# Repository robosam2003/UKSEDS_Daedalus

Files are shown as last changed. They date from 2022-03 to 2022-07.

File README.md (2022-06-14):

# UKSEDS Team Daedalus - "In thrust we trust"

The rocket avionics consisted of a Teensy 4.1 for the main microcontoller, a low-g IMU (BNO055), a high-g accelerometer (ADXL377), a pressure sensor (BMP280), a GPS (NEO-6M) and a 433 MHz radio transciever (RFM96W).

The purpose of the rocket was to collect acceleration and gyroscope data such that we could test our IMU based position estimation algorithm (also called dead reckoning).

# Code
The `code` folder contains code for all the sensors and telemetry onboard and for the ground station. The `masterCode` folder contains the final code loaded onto the rocket.

## Sensors and telemetry:
- **BNO055**: Our low-g IMU, containing accelerometers capable of ±16G, as well as very accurate gyroscopes and magnetometers. Big thanks to SunrIde's [Tom Danvers](https://github.com/TomD53) for writing the library we used to interface with the BNO055: [`Arduino-BNO055`](https://github.com/TeamSunride/Arduino-BNO055). 
- **ADXL377**: Our high-g IMU, capable of up to ±200G. This is an analogue sensor and is *very noisy*, so both hardware filters (capacitors) and software filters ([Kalman filters](https://github.com/denyssene/SimpleKalmanFilter)) were used to get accurate data. 
- **BMP280**: A pressure based altimeter used in conjunction with the brilliant [Adafruit library](https://github.com/adafruit/Adafruit_BMP280_Library).
- **NEO-6M**: A cheap but capable GPS module from ublox. In order to get a fast GPS lock, we implemented assisted GPS loading using the ublox AssistNow service. See [`code/NEO6mWithAssistNow`](https://github.com/robosam2003/UKSEDS_Daedalus/tree/main/code/NEO6mWithAssistNow).
- **RFM96W**: A 433MHz SX1272 based tranciever module that was used both onboard and on our ground station. We used the LoRa protocol for greater range. We implemented an interrupt driven method using [`RadioLib`](https://github.com/jgromes/RadioLib).

## Ground station
The ground station used an old arduino nano with the RFM96W to recieve live telemetrics from the rocket. The launch commit button was used to put the rocket into a launch ready state remotely.

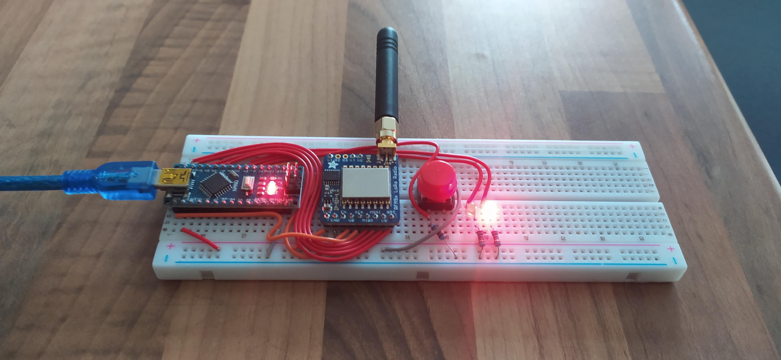
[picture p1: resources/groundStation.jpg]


It passed this data to Grafana and InfluxDB using the [line protocol](https://docs.influxdata.com/influxdb/cloud/reference/syntax/line-protocol/). Big thanks to SunrIde's [Yomi](https://github.com/abayomi185), [Tom](https://github.com/TomD53) and [Sebastiano](https://github.com/robosam2003/UKSEDS_Daedalus/blob/main/resources/grafanaDashboard.jpg) for building the software to do this [`TeamSunride/GroundStation`](https://github.com/TeamSunride/GroundStation). Our live telemetry Grafana Dashboard is shown below:

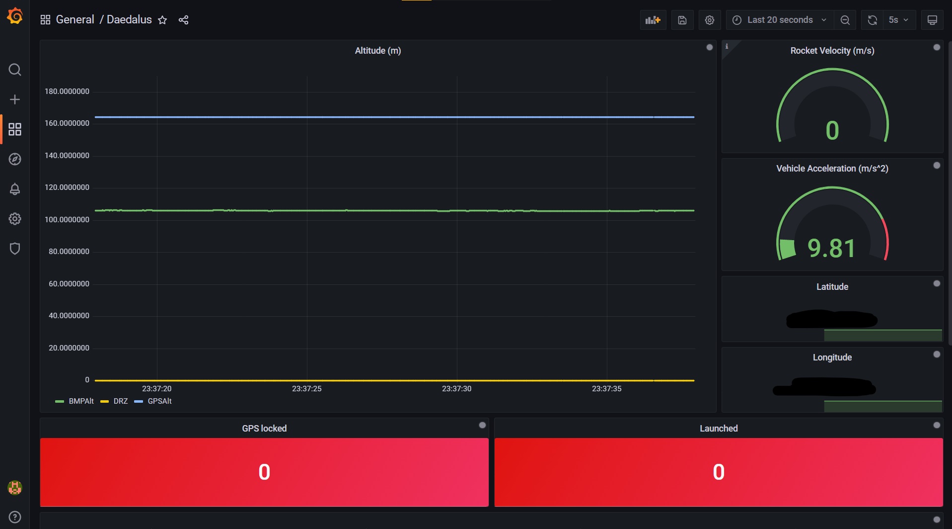
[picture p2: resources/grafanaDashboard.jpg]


### The rocket launch sequence is as follows:
- Ensure ground station is booted and ready.
- **Compile** masterCode/main.cpp and upload to teensy so that the RTC syncs.
- Setup sensors, datalogging and telemety on the ground.
- Full system test with serial output to double check sensor values look reasonable.
- Load avionics into rocket.
- Wait for "Launch commit" from ground station.
- When rocket is loaded on the launch rail, press launch commit button on ground station (wait for confirmation - ground station light should go green).
- Start data acquisition, datalogging and transmitting data.
- Launch!

Loading avionics:

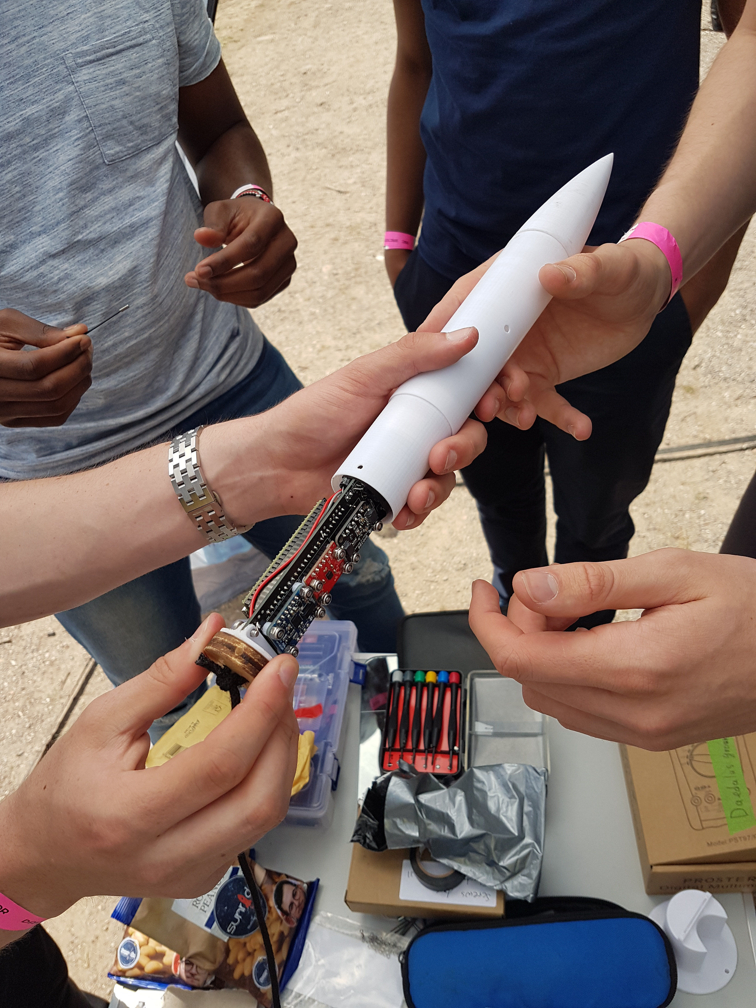
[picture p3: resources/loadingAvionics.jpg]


# Circuitry
This rocket used breakout boards to house components. This made testing and verification easier before ordering the final PCB. The PCB was designed in EAGLE using many custom libraries. 

The final schematic:

[`Rocketry_circuit.sch`](https://github.com/robosam2003/UKSEDS_Daedalus/blob/main/circuitry/Rocketry_circuit.sch):

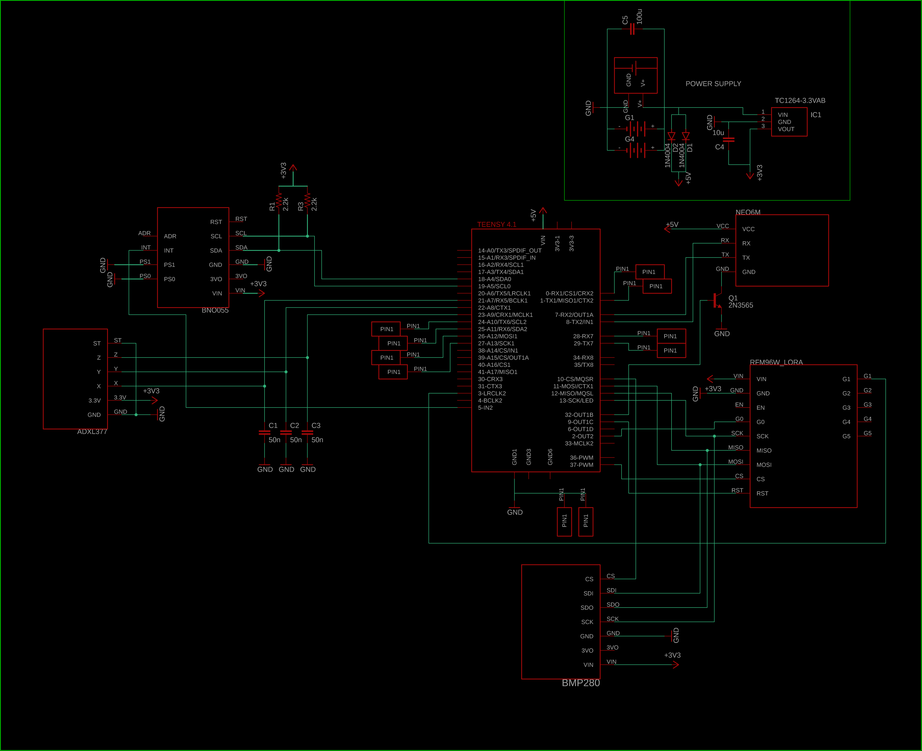
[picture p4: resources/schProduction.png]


The final pcb board design:

[`Rocketry_circuit.brd`](https://github.com/robosam2003/UKSEDS_Daedalus/blob/main/circuitry/Rocketry_circuit.brd):

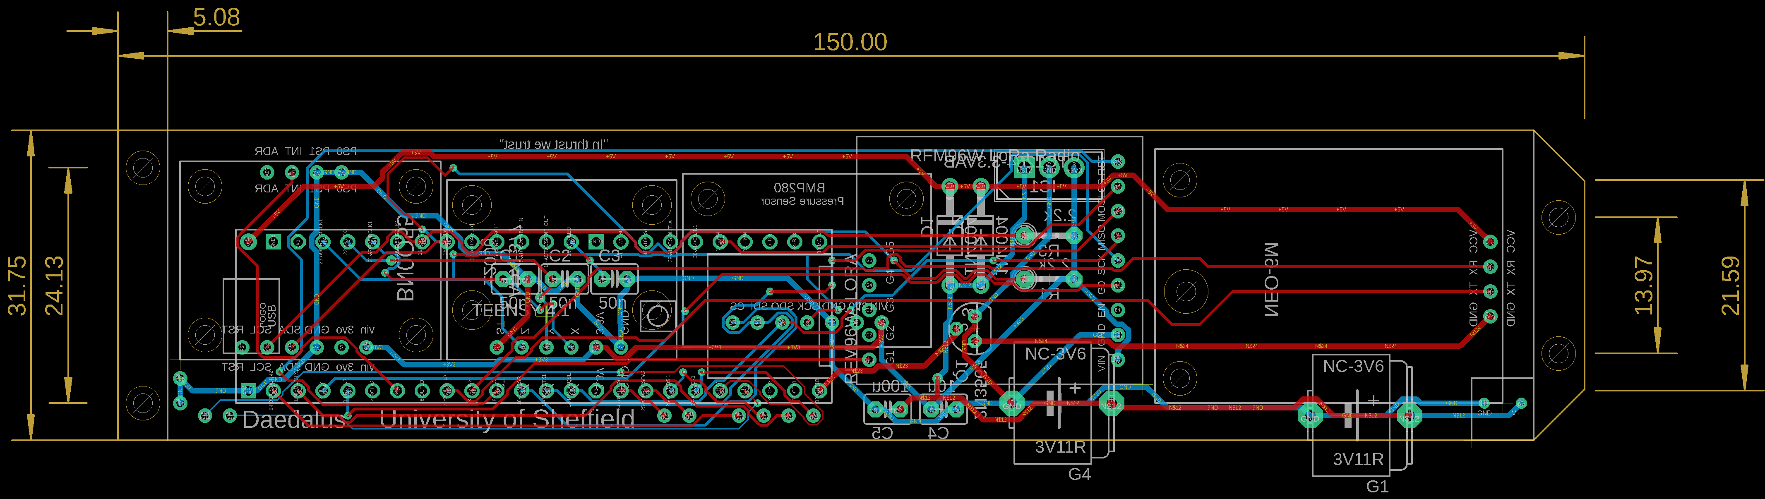
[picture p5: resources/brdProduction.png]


The manufactured PCB (from china):   

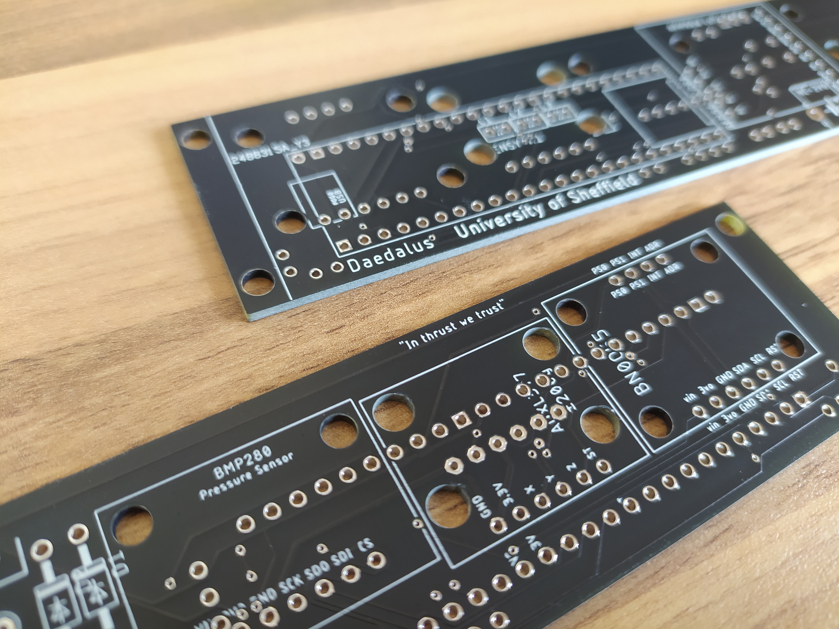
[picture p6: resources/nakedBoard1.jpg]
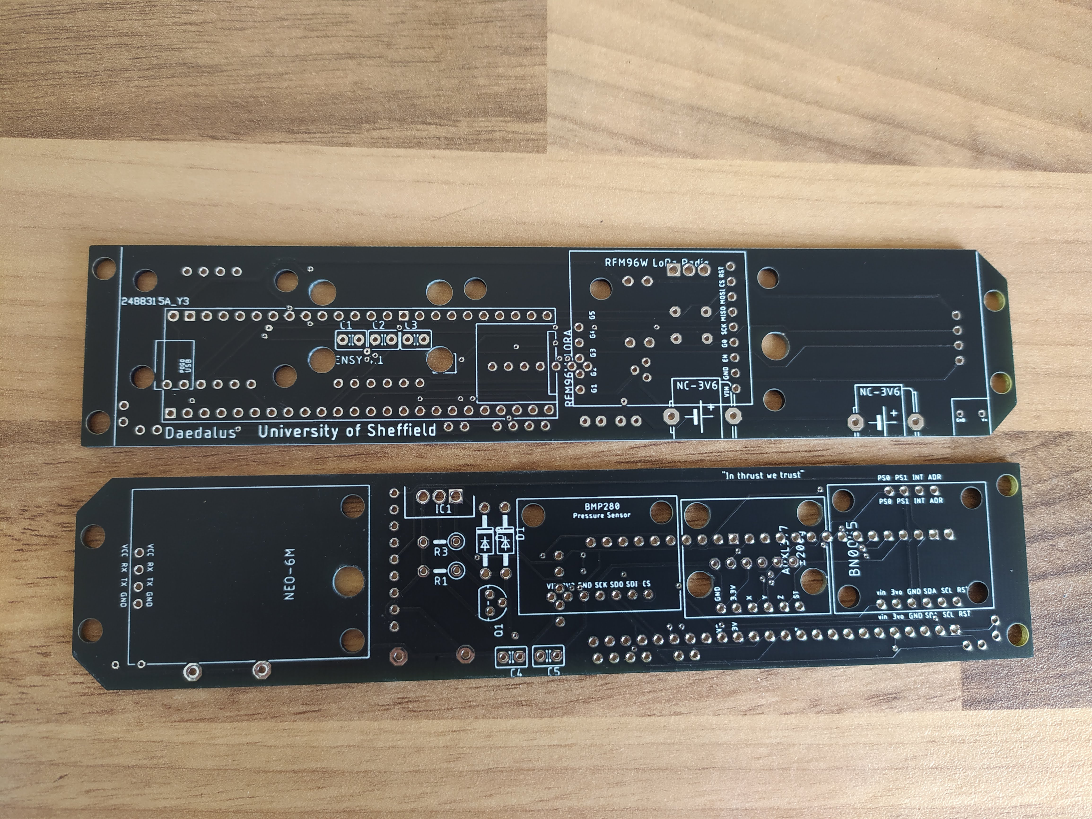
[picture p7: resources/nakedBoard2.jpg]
 

The assembled pcb with breakouts soldered and mounted:

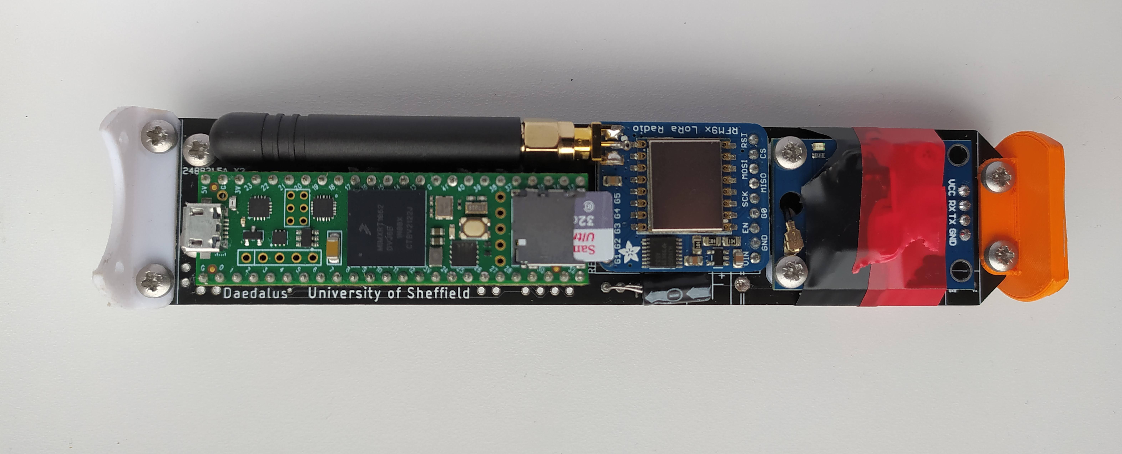
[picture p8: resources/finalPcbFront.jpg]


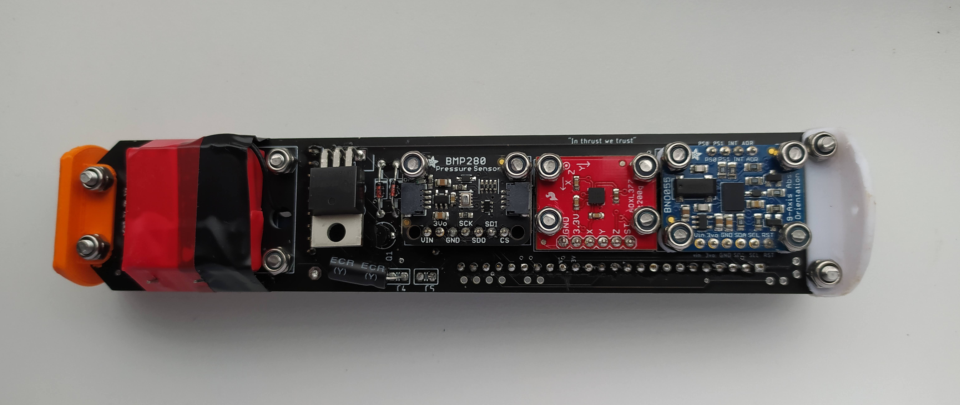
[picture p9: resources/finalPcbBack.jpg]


The avionics recovered after flight:

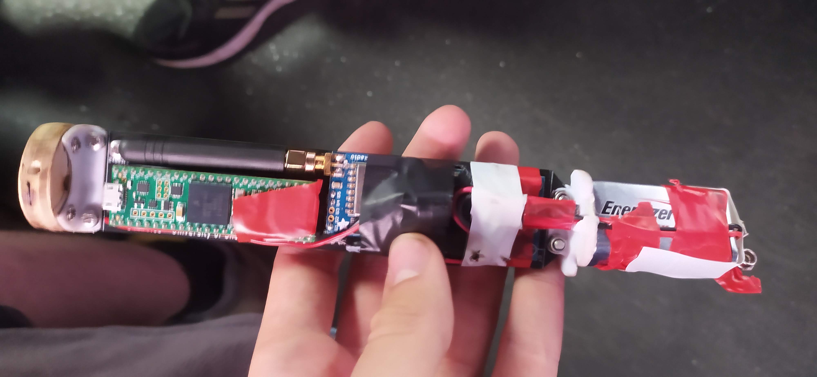
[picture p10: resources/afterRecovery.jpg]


# Flight data

The launch was a ~success!~... it *went up* anyway. We suspect excess friction on the launch rail caused it to fly off course at about a 45° angle. (See https://www.youtube.com/watch?v=rMJzLpDIJ3U)

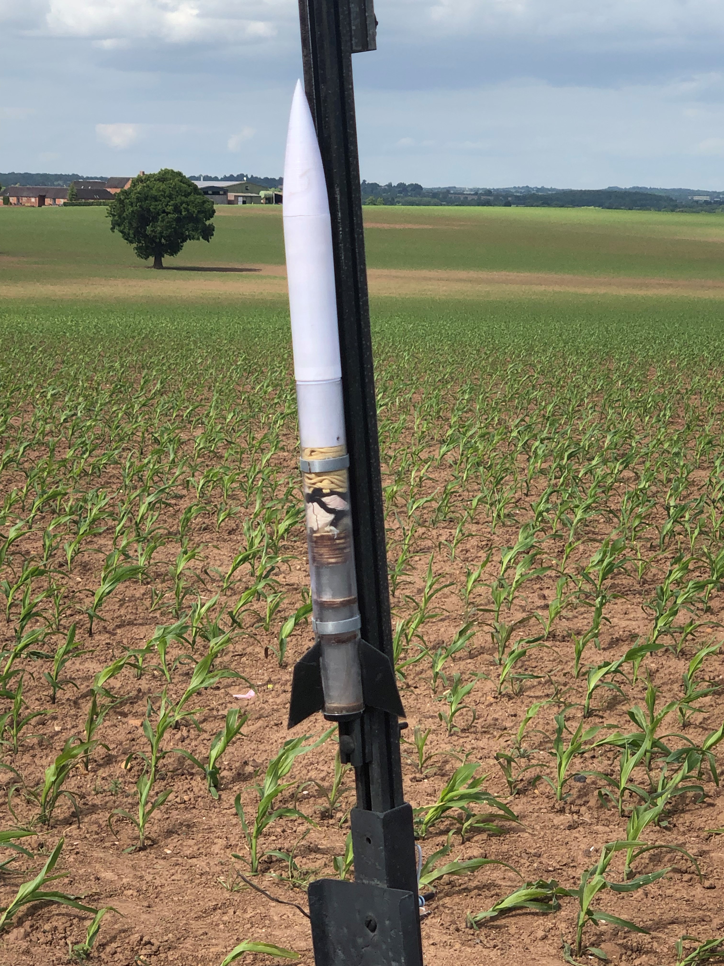
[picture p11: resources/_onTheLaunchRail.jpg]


The rocket still achieved an apogee of 641m according to the BMP280 altimeter (note that the spike at apogee caused by the pressure from the ejection charge). The GPS lost satellite lock on launch as predicted, but regrained lock after apogee:

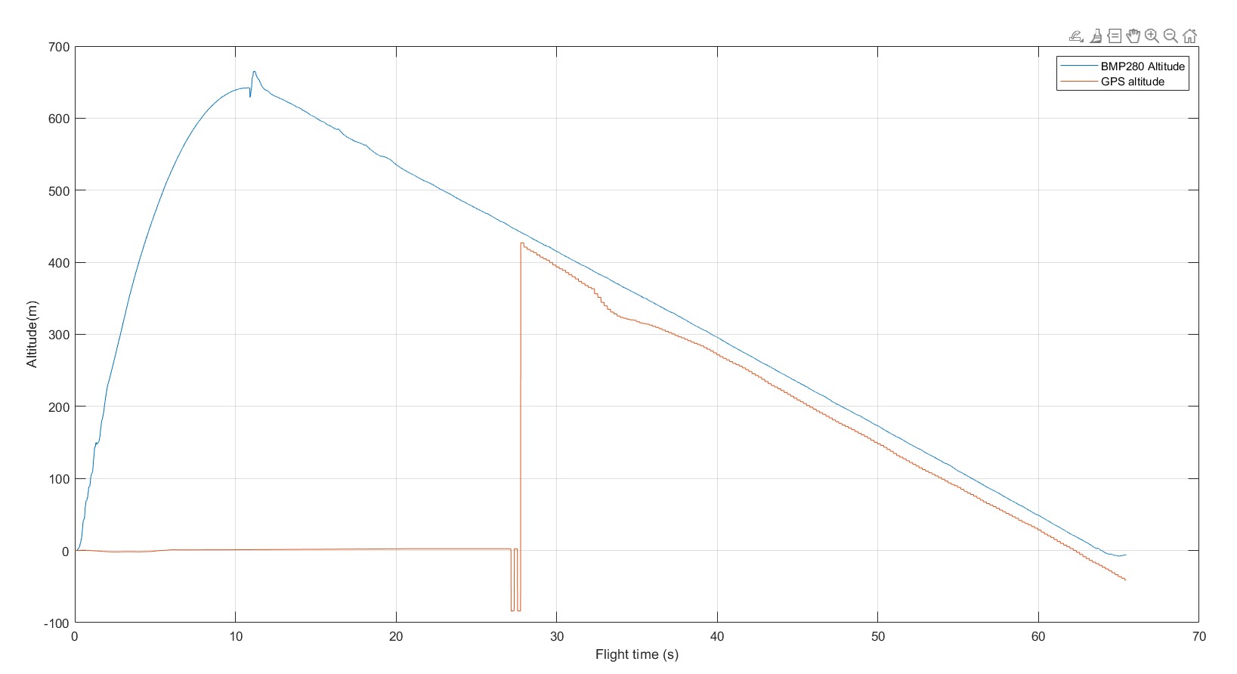
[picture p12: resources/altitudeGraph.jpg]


The acceleration data followed our expectations from the OpenRocket simulation, with a slightly lower max acceleration of 14.4g. Unfortunately, the BNO055 maxed out at 4G, rather than the desired 16g, despite having configured it to read up to 16g. The ADXL377 data is decent though: (note the spike at ejection charge)
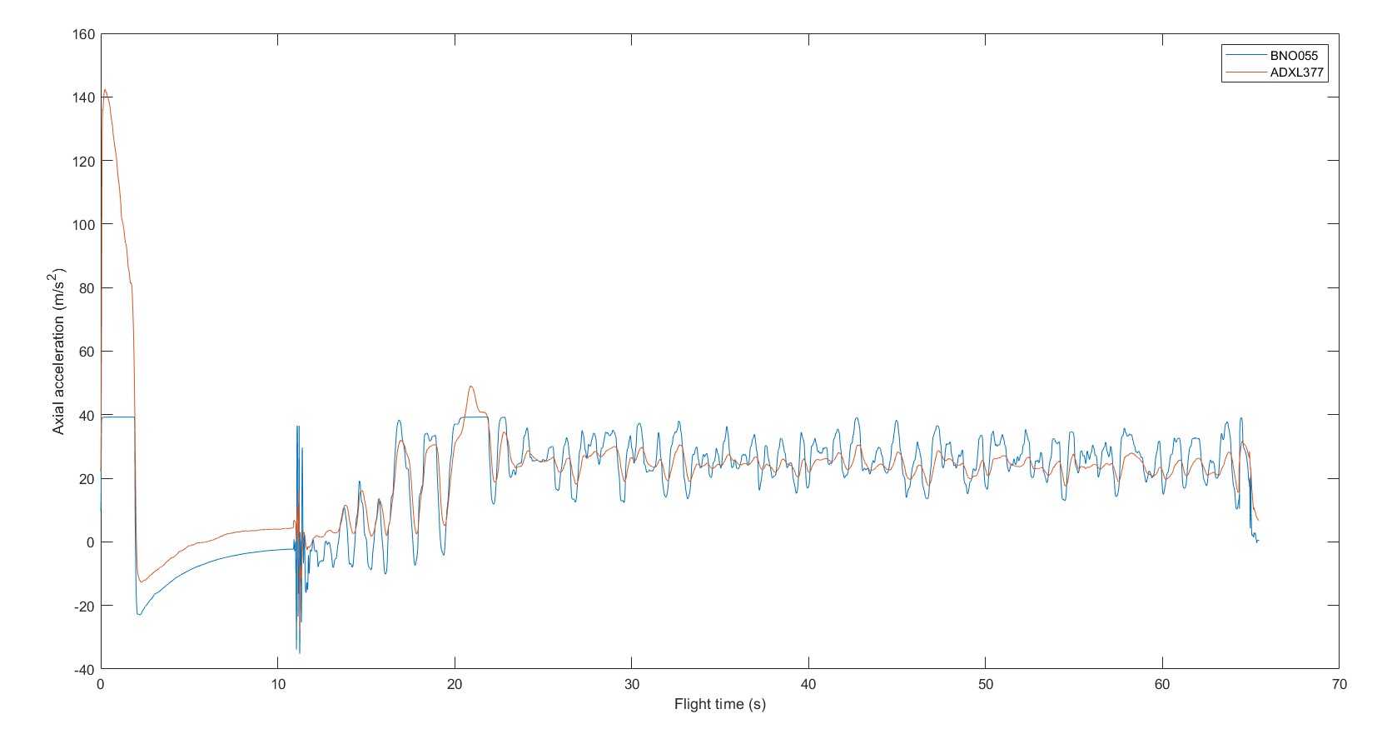
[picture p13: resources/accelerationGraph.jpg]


The onboard dead reckoning algorithm also didn't work as expected, due to the BNO055 maxing out earlier than anticipated and due to the initial launch being so oscillatory (which threw off orientation estimation) the data is not an accurate measurement of position. Much has been learned from this launch and will be refined in future rockets. :)

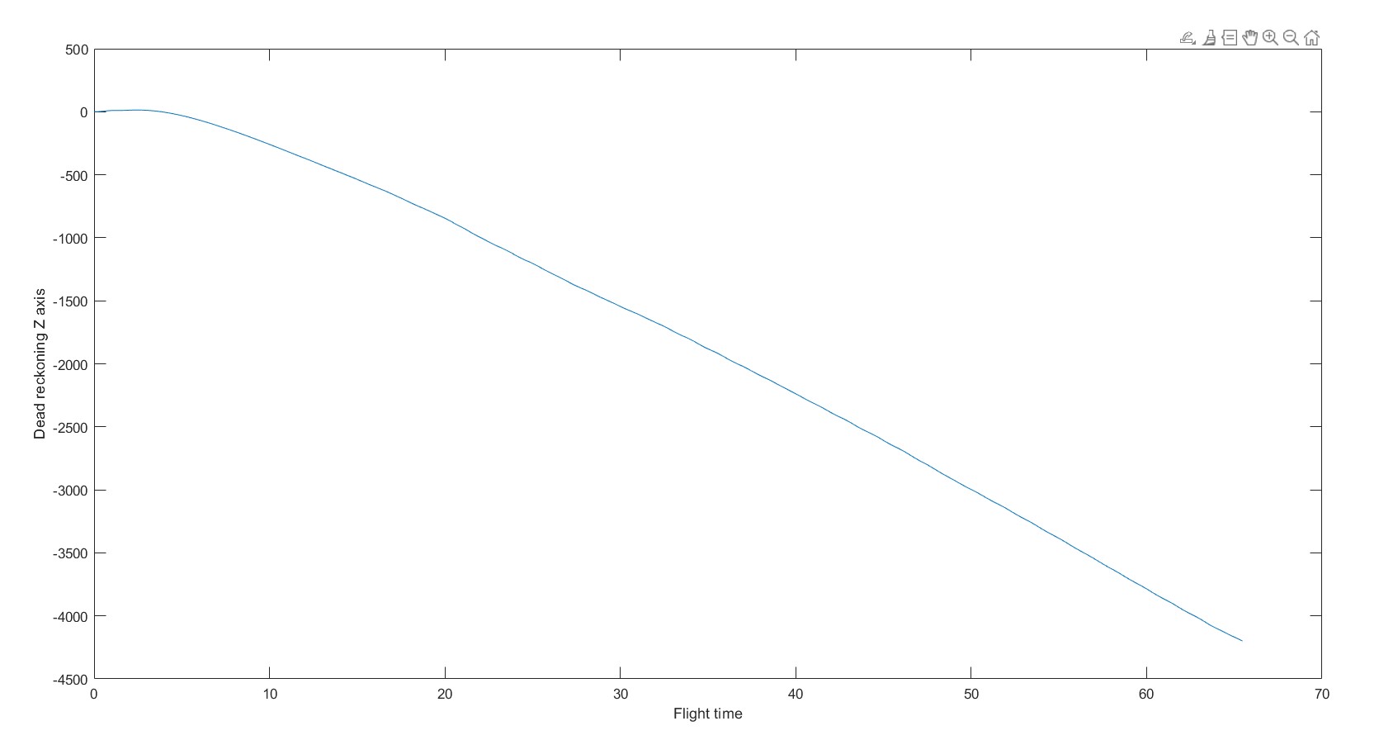
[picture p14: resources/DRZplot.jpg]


The **telemetry** range was not very good, likely due to bad antennas, and because of UK regulations which limited our transmit power down to 10dbm at a max duty cycle of 10%. :(

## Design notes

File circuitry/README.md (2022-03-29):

This is the folder for circuitry

.brd files contain files relating to pcb placement and copper routing

.sch files contain schematics\n

.pro files contin autorouter data\n

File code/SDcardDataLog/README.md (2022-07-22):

- Note: using exFat formatting slows things down

- Use ringbuff to write to files mega fast - 40us for 512 bytes as per my testing on teensy 4.1 using SDIO

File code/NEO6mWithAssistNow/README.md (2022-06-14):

# NEO-6M with AssistNow loading

### Links:
- [Datasheet](https://content.u-blox.com/sites/default/files/products/documents/u-blox6_ReceiverDescrProtSpec_%28GPS.G6-SW-10018%29_Public.pdf)

- [Ublox GNSS Assistance user guide](https://content.u-blox.com/sites/default/files/products/documents/MultiGNSS-Assistance_UserGuide_%28UBX-13004360%29.pdf)

- To get started with using Ublox servers for assisted GPS, see [assistnow-getting-started-guide](https://developer.thingstream.io/guides/location-services/assistnow-getting-started-guide).

#

These modules use the UBX protocol to communicate with the GPS, in this case, over a UART connection.

There is a lot of configuration that can be done with these modules, but the important ones are demonstrated in `NEO6mConfig()`. The message classes and types are outlined in `assistNow.h`.

The main advantage of setting up the GPS in this way is that it allows for configuration using **assisted GPS** - called **AssistNow** for Ublox GPS modules - which allows for ultrafast GPS satellite lock - a serious problem for many GPS modules, especially cheap ones like the NEO6m.

The UBX protocol structure is as follows:

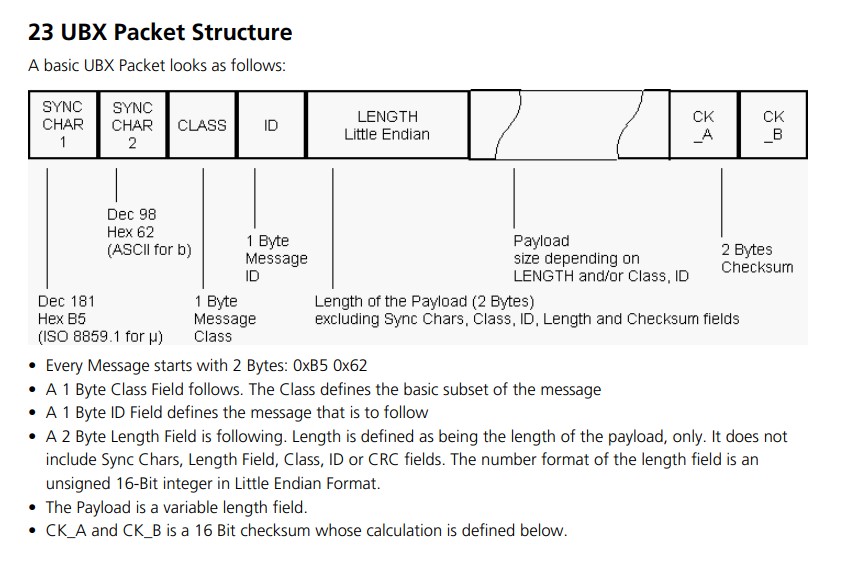
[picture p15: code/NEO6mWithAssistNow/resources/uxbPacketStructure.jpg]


The CFG messages set up the GPS for use, and the other message classes are used for things like aiding, acknowledgements, and getting raw data. Note that the CFG messages will send a ACK(acknowledged) or NAK(not acknowledged) message back to the GPS for CFG messages, the `sendUBX()` function deals with this. See the datasheet for more information.

## Usage

If a message is set up with *periodic polling*, it will be sent every `measrate` milliseconds:
```cpp
    delay(measrate);
    getGPSData(); // For if the NAV-POSLLH message is set up to be periodic
```

Otherwise, sending an empty payload will 'poll' the GPS for the message:
```cpp
    sendUbx(NAV, NAV_POSLLH, 0, nullptr); // Sending

    delay(measrate);  // GPS is confifured for 5Hz update rate
    
    getGPSData(); // For NAV-POSLLH message
```

## AssistNow loading
To perform AssistNow loading, first get the `mgaonline.ubx` file from the ublox server (see [`assistnow-getting-started-guide`](https://developer.thingstream.io/guides/location-services/assistnow-getting-started-guide)), load it an SD card and insert the SD card into the teensy.

Ensure you *compile* the program such that the teensy RTC syncs and the `getTimestampMillis()` function works as expected - **An accurate timestamp is vital to get a quick satellite lock**

The `performOnlineAssist()` function will load the file and send it to the GPS, modifying the timestamp field. If the Almanac and Ephemeris are valid, then this will greatly improve GPS lock time.

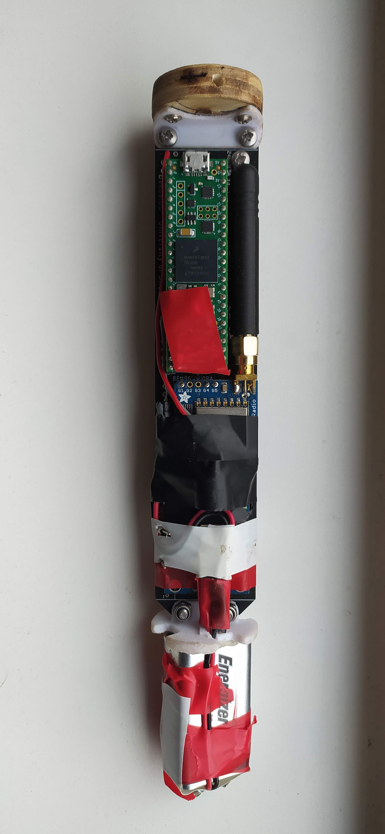
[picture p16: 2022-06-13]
resources/avionicsafterFlight.jpg

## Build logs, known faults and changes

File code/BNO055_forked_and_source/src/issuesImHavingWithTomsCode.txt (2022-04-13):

- Consider replacing custom-made Vector.h with:  https://github.com/janelia-arduino/Vector
    - I've added some operators ([]) to the Vector.h file

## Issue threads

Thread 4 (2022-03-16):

Processes things too slow

robosam2003, 2022-03-16:
Try increasing teensy clock speed? SD card writes are pretty slow

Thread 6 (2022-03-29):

Transmission over serial is slow - limits max transmission rate for telemetry.

robosam2003, 2022-03-29:
Look into the max baud rate of the nano, 500KHz?

https://arduino.stackexchange.com/questions/296/how-high-of-a-baud-rate-can-i-go-without-errors

robosam2003, 2022-04-06:
It is pretty fast if you do it as a single string - 500us or so.

Closed 2022-04-06.

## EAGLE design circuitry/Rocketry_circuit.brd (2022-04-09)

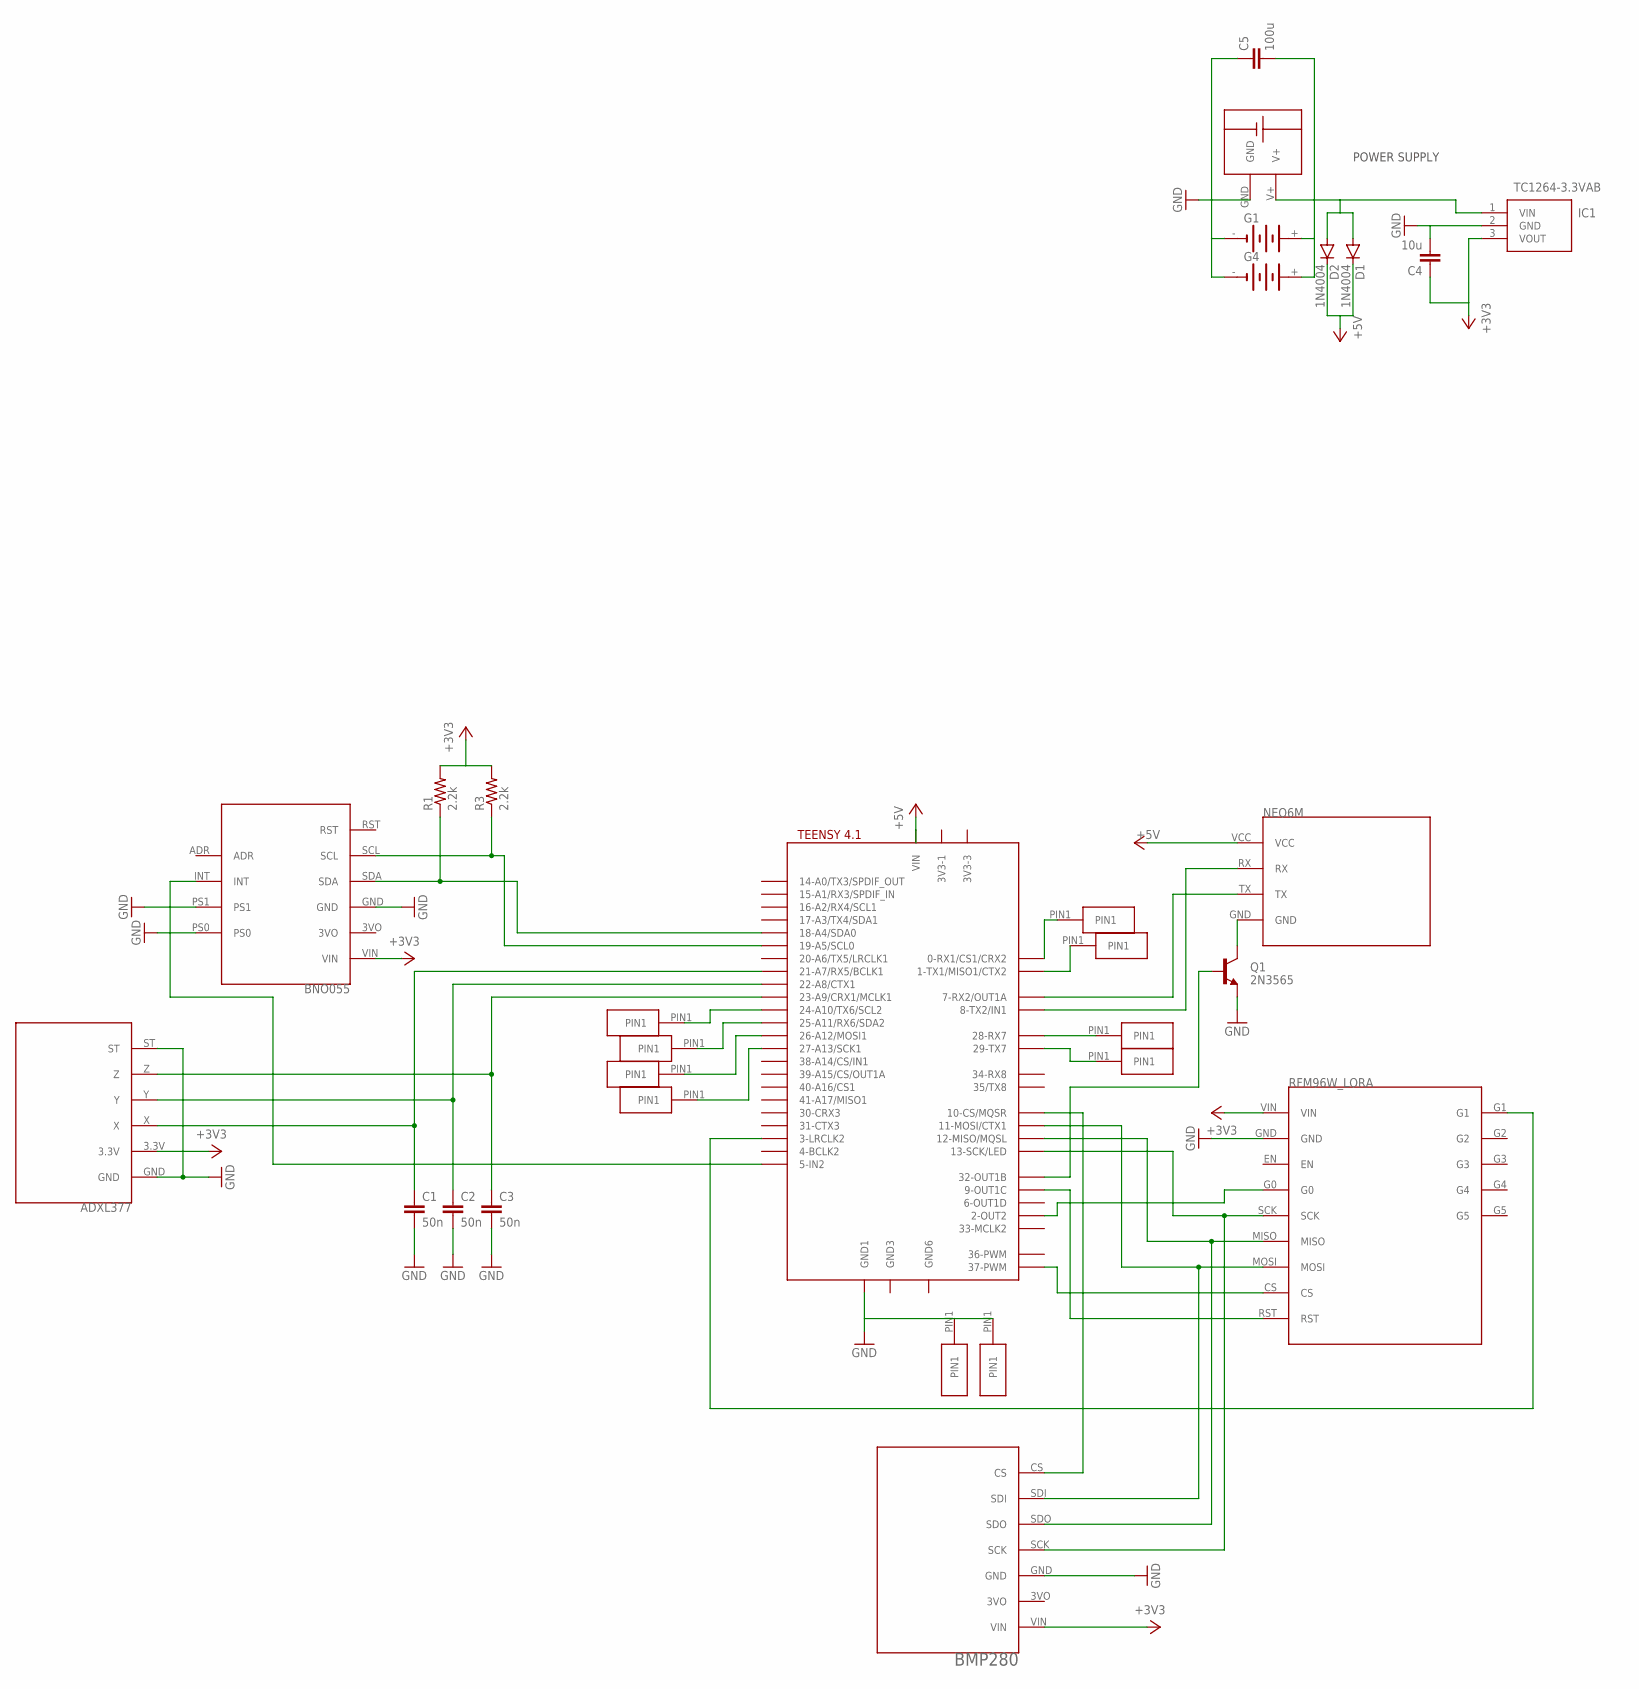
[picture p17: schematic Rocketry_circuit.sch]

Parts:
BRKOUT1: BNO055
C1, C2, C3: 50n; C2.5-3
C4: 10u; C2.5-3
C5: 100u; C2.5-3
D1, D2: 1N4004; DO41-10
G1, G4: 3V11R
IC1: TC1264-3.3VAB; TO254P483X988X2222-3P
Q1: 2N3565; TO92
R1, R3: 2.2k; 0207/5V
U$1: TEENSY41
U$2: BMP280
U$3: ADXL377
U$4: NEO6M
U$5: RFM96W
U$6, U$7, U$8, U$9, U$10, U$11, U$13, U$14, U$15, U$16: 1PINOUT
U$12: SMALL_SCREW_TERMINAL

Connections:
+3V3: BRKOUT1.VIN, C4.1, IC1.3 (VOUT), R1.2, R3.2, U$2.VIN, U$3.3.3V, U$5.VIN
+5V: D1.C, D2.C, U$1.VIN, U$4.VCC
GND: BRKOUT1.GND, BRKOUT1.PS0, BRKOUT1.PS1, C1.2, C2.2, C3.2, C4.2, C5.1, G1.-, G4.-, IC1.2 (GND), Q1.3 (E), U$1.GND1, U$2.GND, U$3.GND, U$3.ST, U$5.GND, U$10.PIN1, U$11.PIN1, U$12.GND
unnamed: C1.1, U$1.21-A7/RX5/BCLK1, U$3.X
unnamed: C2.1, U$1.22-A8/CTX1, U$3.Y
unnamed: BRKOUT1.SDA, R1.1, U$1.18-A4/SDA0
unnamed: C3.1, U$1.23-A9/CRX1/MCLK1, U$3.Z
unnamed: BRKOUT1.SCL, R3.1, U$1.19-A5/SCL0
unnamed: U$1.7-RX2/OUT1A, U$4.TX
unnamed: U$1.8-TX2/IN2 (8-TX2/IN1), U$4.RX
unnamed: U$1.13-SCK/LED, U$2.SCK, U$5.SCK
unnamed: U$1.12-MISO/MQSL, U$2.SDO, U$5.MISO
unnamed: U$1.11-MOSI/CTX1, U$2.SDI, U$5.MOSI
unnamed: U$1.37-PWM, U$5.CS
unnamed: C5.2, D1.A, D2.A, G1.+, G4.+, IC1.1 (VIN), U$12.V+
unnamed: BRKOUT1.INT, U$1.5-IN2
unnamed: U$1.2-OUT2, U$5.G0
unnamed: U$1.24-A10/TX6/SCL2, U$9.PIN1
unnamed: U$1.10-CS\MQSR (10-CS/MQSR), U$2.CS
unnamed: U$1.25-A11/RX6/SDA2, U$7.PIN1
unnamed: U$1.28-RX7, U$6.PIN1
unnamed: U$1.3-LRCLK2, U$5.G1
unnamed: U$1.9-OUT1C, U$5.RST
unnamed: U$1.29-TX7, U$8.PIN1
unnamed: U$1.26-A12/MOSI1, U$13.PIN1
unnamed: Q1.2 (B), U$1.32-OUT1B
unnamed: Q1.1 (C), U$4.GND
unnamed: U$1.27-A13/SCK1, U$14.PIN1
unnamed: U$1.0-RX1/CS1/CRX2, U$15.PIN1
unnamed: U$1.1-TX1/MISO1/CTX2, U$16.PIN1

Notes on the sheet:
POWER SUPPLY

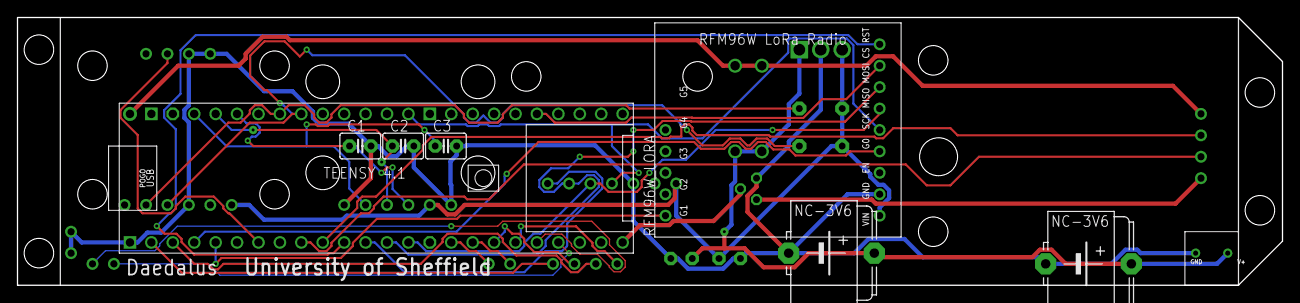
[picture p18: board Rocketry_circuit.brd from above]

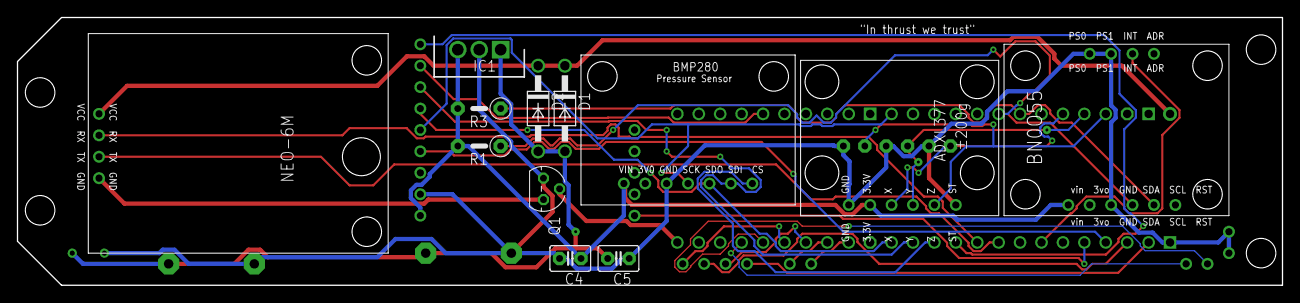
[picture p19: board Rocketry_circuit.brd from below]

Board: 2 copper layers, 150.0 x 31.8 mm, 30 parts (12 on the bottom side), 30 nets.

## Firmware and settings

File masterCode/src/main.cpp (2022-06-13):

#include "C:\Users\robos\CLionProjects\UKSEDS_Daedalus\code\ADXL377\src\ADXL377.h"
#include "C:\Users\robos\CLionProjects\UKSEDS_Daedalus\code\BNO055_forked_and_source\src\BNO055daedalus.h"
#include "C:\Users\robos\CLionProjects\UKSEDS_Daedalus\code\SDcardDataLog\src\SDcardDataLog.h"
#include "C:\Users\robos\CLionProjects\UKSEDS_Daedalus\code\NEO6mWithAssistNow\src\NEO6mWithAssistNow.h"

// I have absolutely no idea why just I cant just include the .h file JUST for the transmitter, but hey-ho - quick fix, it works
#include "C:\Users\robos\CLionProjects\UKSEDS_Daedalus\code\RFM96W_Transmitter_LoRa\src\RFM96WtransmitLORA.h"
#include "C:\Users\robos\CLionProjects\UKSEDS_Daedalus\code\RFM96W_Transmitter_LoRa\src\RFM96WtransmitLORA.cpp"
//#include "C:\Users\robos\CLionProjects\UKSEDS_Daedalus\code\RFM96W_Reciever_LoRa\src\RFM96WrecieveLORA.h"
//#include "C:\Users\robos\CLionProjects\UKSEDS_Daedalus\code\RFM96W_Reciever_LoRa\src\RFM96WrecieveLORA.cpp"

#include "C:\Users\robos\CLionProjects\UKSEDS_Daedalus\code\BMP280\src\BMP280.h"

/** Global variables defined in other files:
 * - BNO055daedalus.h
 *   - BNO055 sensor(BNO055_I2C_ADDRESS, &Wire) 
 *   - Vector<double> acc_biases
 *   - Vector<double> gyr_biases
 *   - double prevVect[numDR][9]
 *   - Vector<double> omegaAverage
 *   - Vector<double> accAverage
 *   - double biasAverageOmegaThreshold
 *   - double biasAverageAccThreshold
 *   - Vector<double> pos
 *   - Vector<double> vel
 *   - Vector<double> ori
 *   - int DRcounter
 *   - SimpleKalmanFilter filteredAccBNO055X
 *   - SimpleKalmanFilter filteredAccBNO055Y
 *   - SimpleKalmanFilter filteredAccBNO055Z
 *   - SimpleKalmanFilter filteredGyroX
 *   - SimpleKalmanFilter filteredGyroY
 *   - SimpleKalmanFilter filteredGyroZ
 *   - Vector<double> filteredAccBNO055
 *   - Vector<double> filteredGyro
 *   - Vector<double> trueAccVect
 * - ADXL377.h
 *   - Vector<double> filteredAccADXL377_X
 *   - Vector<double> filteredAccADXL377_Y
 *   - Vector<double> filteredAccADXL377_Z
 *   - Vector<double> filteredADXL
 *   - float ADXLscale
 *   -
 *
 *
 *
 *
 * - NEO6mWithAssistNow.h
 *   - GPSDataStruct GPSData
 *   -
 *
 *
 *
 * - SDcardDataLog.h
 *
 *
 */
byte statusCode = 0b00000000; // This can be altered to show various stages of the launch FOR SD CARD

double SEA_LEVEL_HPA = 1010; // CHANGE TO LOCAL FORECAST

// Transmittsion/reception codes - FOR TRANSMISSION
#define RTC_SYNC_BYTE 0x99
#define TEST_CODE 0xAA
#define LAUNCH_COMMIT_CODE 0xBB
#define LAUNCH_COMMIT_CONFIRM 0xCC
#define DATA_CODE 0xDD
unsigned long long cycleCounter = 0;
bool launched = false;

double launchThreshold = 2*9.81;

#define LAUNCH_DETECT_MASK 0b00000001   

#define buzzerPin 24

void fullSystemTest() {
    // Tests each subsystem for several seconds. 
    // Do this just before launch, Use HTERM for terminal input.
    Serial.printf("---------- FULL SYSTEM TEST ----------\n\n");

    Serial.printf("Timestamp test...\n");
    delay(500);
    for (int i=0; i<10; i++) {
        uint64_t ts = getTimestampMillis();
        Serial.printf("UNIX TIME: %llu\n", ts);
        delay(100);
    }
    Serial.printf("Timestamp test complete.\n");
    enterToContinue();

    Serial.printf("Testing BNO055 for 10 Seconds... \n");
    delay(500);
    for (int i=0; i<10*100; i++) {
        bno055_burst_t burst = sensor.getAllData();
        Vector<double>rawBNO055Acc = burst.accel;
        Vector<double>rawBNO055Gyro = burst.gyro;
        for(int i=0;i<3;i++) { rawBNO055Acc[i] -= acc_biases[i];  rawBNO055Gyro[i] -= gyr_biases[i]; }

        updateBNOFilters(rawBNO055Gyro, rawBNO055Acc);
        Serial.printf("BNO055 RAW - acc: (x, y, z) %lf, %lf, %lf     gyro : (x, y, z) %lf, %lf, %lf\n",
                      rawBNO055Acc[0], rawBNO055Acc[1], rawBNO055Acc[2],
                      rawBNO055Gyro[0], rawBNO055Gyro[1], rawBNO055Gyro[2]);
        delay(10);
    }
    Serial.printf("BNO055 test complete.\n");
    enterToContinue();

    Serial.printf("Testing ADXL377 for 15 Seconds... \n");
    delay(500);
    for (int i=0; i<15*100; i++) {
        uint32_t start = micros();
        Vector<double> rawADXLacc = getADXL377Acc();
        updateADXL377Filters(rawADXLacc);
        Serial.printf("ADXL377 filtered - acc: (x, y, z) %lf, %lf, %lf\n",
                      filteredADXL[0], filteredADXL[1], filteredADXL[2]);
        uint32_t end = micros();
        delayMicroseconds( ((end-start) < cycleTimeus ) ? (cycleTimeus- (end - start) ) : 0 );
    }
    
    Serial.printf("ADXL377 test complete.\n");
    enterToContinue();

    Serial.printf("Testing RFM96W transmission for 15 Seconds... \n");
    //delay(500);
    for (int i=0; i<200; i++) {
        byte data[23] = {};
        data[0] = 0xAA;
        while(!transmittedFlag);
        transmitData(data);
        Serial.printf("Successfully transmitted data.\n");
        delay(30);
    }

    Serial.printf("Testing NEO6m...\n");
    enterToContinue();
    Serial.printf("Testing NEO6m. Press enter to exit loop (when locked)\n");
    delay(500);
    Serial.clear();
    while(1) {
        if (Serial.available()){
            Serial.printf("Entering main loop.\n");
            break;
        }
        sendUbx(NAV, NAV_POSLLH, 0, nullptr);
        delay(200);
        getGPSData();
        Serial.printf("\nTOW:        %d\n", GPSdata.towMs);
        Serial.printf("Actual TOW: %d\n", actualTimeOfWeekms());
        Serial.printf("Time %d:%d:%d\n", hour(), minute(), second());
        Serial.printf("LONG: %lf\n", GPSdata.lon);
        Serial.printf("LAT: %lf\n", GPSdata.lat);
        Serial.printf("HMSL(m): %lf\n", GPSdata.alt);
        Serial.printf("HACC(m): %d\n", GPSdata.hAcc / 1000);
        Serial.printf("VACC(m): %d\n", GPSdata.vAcc / 1000);
        
    }
    Serial.clear();




}

void groundRTCSync() {
    //radio.setDio0Action(setFlag);
    u_int64_t unixTime = getTimestampMillis();
    Serial.printf("UNIX TIME: %llu\n", unixTime);
    byte arr[lenTransmissionBytes] = {RTC_SYNC_BYTE};
    for (int i=0; i<8; i++) {
        arr[i+1] = (unixTime >> (7 * 8 - (i * 8))) & 0xFF; // little endian
    }
    while(!transmittedFlag); // transmittedFlag should be true here.
    transmitData(arr);
    Serial.printf("Successfully transmitted UNIX TIME to ground station.\n");



}

void setup() {
    Serial.begin(115200);
    delay(500);

    enterToContinue();

    Serial.printf("-------------INITIALIZING SENSORS------------\n");

/** Initialise sensors:
     *  - BNO055
     *  - ADXL377
     *  - BMP280
     *  - GPS  */
    BMP280Setup();
    NEO6mSetup();
    BNO055Setup();
    ADXL377Setup();


/** Initialise SD card and transmitter */
    unsigned long long timestampSDFileName = getTimestampMillis();
    sdSetup(timestampSDFileName);
    
    RFM96WtransmitSetup();
    Serial.printf("SUCCESS - All systems initialised.\n");

/** Send Teensy unix time to ground station over telemetry to sync. */
    Serial.printf("SYNCING ground station RTC\n");
    groundRTCSync();

    enterToContinue();
    

/** Full system test before launch */
    fullSystemTest();




/** Wait for "Launch commit" message from ground station */
    // Set up RFM96W as receiver
    radio.setDio0Action(setFlagRecieve);

    // Wait for Launch commit message
    bool launchCommit = false;
    while (!launchCommit) {
        Serial.println("Waiting for launch commit code from ground station...");
        int state = radio.startReceive();
        while(!receivedFlag); // wait for packet
        state = radio.readData(byteArr, lenTransmissionBytes);
        //RFM96WrecieveBytesLORA();
        Serial.println("Received message");
        if (byteArr[0] == LAUNCH_COMMIT_CODE) {
            launchCommit = true;
            Serial.println("Launch commit message received");
        }
        else {
            Serial.println("That wasnt the launch commit code");
        }
    }
    delay(500);
    // Set up RFM96W as transmitter
    radio.setDio0Action(setFlag);
    // Send confirmation message to ground station
    char launchCommitMessasge[23] = {LAUNCH_COMMIT_CONFIRM, 0,0,0,0,0,0,0};
    transmissionState = radio.startTransmit(launchCommitMessasge);
    Serial.println("Sent launch commit confirmation");


// The dreaded code that caused far too many hours of debugging - do not touch :)
// /** Wait for "Launch commit" message from ground station */
//     // Set up RFM96W as receiver
//     radio.setDio0Action(setFlagRecieve);
//     // Wait for Launch commit message
//     bool launchCommit = false;
//     while (!launchCommit) {
//         Serial.println("Waiting for launch commit code from ground station...");
//         int state = radio.startReceive();
//         while(!receivedFlag); // wait for packet
//         RFM96WrecieveBytesLORA();
//         Serial.println("Received message");
//         if (byteArr[0] == LAUNCH_COMMIT_CODE) {
//             launchCommit = true;
//             Serial.println("Launch commit message received");
//         }
//         else {
//             Serial.println("That wasnt the launch commit code");
//         }
//     }
//     delay(1000);
//     // Set up RFM96W as transmitter
//     radio.setDio0Action(setFlag);
//     // Send confirmation message to ground station
//     byte launchCommitMessasge[23] = {LAUNCH_COMMIT_CONFIRM, 0,0,0,0,0,0,0}; // TODO: this is not working??? 
//     //transmissionState = radio.startTransmit(launchCommitMessasge);
//     while(!transmittedFlag); // wait for packet
//     transmitData(launchCommitMessasge);
//     Serial.println("Sent launch commit confirmation"); 


// /// We are now on the launch pad, ready to launch.

/** (BNO055) Determine current Orientation using accelerometers and gravity vector*/
    getInitialOrientation();

    Serial.printf("Initial orientation determined: %lf, %lf, %lf \n", ori[0], ori[1], ori[2]);
    launched = false;
    launchInterrupt = false; // for in case the interrupt ran before we got here, due to movement of loading rocket
    // Send GPS request
    sendUbx(NAV, NAV_POSLLH, 0, nullptr);
    delay(200);

    //while(1);

} 

void loop() {
    unsigned long startOfLoopUs = micros();
/** Data acquisition - BNO055, ADXL377, BMP280 */
    // Get timestamp
    uint64_t timestamp = getTimestampMillis();
    
    // Get ADXL377 data
    Vector<double>rawADXLacc = getADXL377Acc();

    // Get and parse BNO055 data
    bno055_burst_t burst = sensor.getAllData();
    Vector<double>rawBNO055Acc = burst.accel;
    Vector<double>rawBNO055Gyro = burst.gyro;

    // Especially for Tom, so he can see the effects that biasing have on dead reckoning results
    SDDataLog.BNO055_acc_x = rawBNO055Acc[0];
    SDDataLog.BNO055_acc_y = rawBNO055Acc[1];
    SDDataLog.BNO055_acc_z = rawBNO055Acc[2];
    SDDataLog.BNO055_gyr_x = rawBNO055Gyro[0];
    SDDataLog.BNO055_gyr_y = rawBNO055Gyro[1];
    SDDataLog.BNO055_gyr_z = rawBNO055Gyro[2];

    // bias correction
    for(int i=0;i<3;i++) { rawBNO055Acc[i] -= acc_biases[i];  rawBNO055Gyro[i] -= gyr_biases[i]; }

    /// Filter updates
    updateBNOFilters(rawBNO055Gyro, rawBNO055Acc);  
    updateADXL377Filters(rawADXLacc);
    tone(buzzerPin, (1000+((int)timestamp%1000)));

    // Launch detection
    if (!launched && ( launchInterrupt || (magnitude(filteredAccBNO055) > launchThreshold) ) ) { 
        // ^ critical efficiency /:)
        launchInterrupt = true;
        launched = true;
        statusCode |= LAUNCH_DETECT_MASK;
    }
    sensor.clearInterrupt();
    //Serial.printf("%d, %d, %lf, %lf\n", launched, launchInterrupt, launchThreshold, magnitude(filteredAccBNO055)); //For testing interrupts and launch detection
    
    // Get BMP280 data
    getBMP280Data(SEA_LEVEL_HPA);

    // Get GPS data every 200ms - 5Hz
    if ((cycleCounter % 20) == 0) {
        getGPSData();
        sendUbx(NAV, NAV_POSLLH, 0, nullptr); // send request for next GPS data, will be available in 200ms (20 cycles)
        SDDataLog.GPS_lat = GPSdata.lat;
        SDDataLog.GPS_lon = GPSdata.lon;
        SDDataLog.GPS_alt = GPSdata.alt;
        SDDataLog.GPS_tow = GPSdata.towMs;
        SDDataLog.GPS_hacc = GPSdata.hAcc;
        SDDataLog.GPS_vacc = GPSdata.vAcc; 
    }

    
/** Calculations */
    if (launched) {
        if (magnitude(filteredAccBNO055) > 14*9.81) { // over 14g, we use the ADXL377 data
            deadReckoning(filteredADXL, filteredGyro, cycleTimeus);
        }
        else {
            deadReckoning(filteredAccBNO055, filteredGyro, cycleTimeus);
        }
    }
    

/** Data logging */
    SDDataLog.logCode = statusCode;
    SDDataLog.timeStamp = timestamp;
    // Raw, (NOT bias corrected) filtered sensor data especially for Tom.
    //   ^ done above, before bias correction

    // Filtered, bias corrected sensor data that is used in dead reckoning
    SDDataLog.BNO055_acc_x_filt = filteredAccBNO055[0];
    SDDataLog.BNO055_acc_y_filt = filteredAccBNO055[1];
    SDDataLog.BNO055_acc_z_filt = filteredAccBNO055[2];
    SDDataLog.BNO055_gyr_x_filt = filteredGyro[0];
    SDDataLog.BNO055_gyr_y_filt = filteredGyro[1];
    SDDataLog.BNO055_gyr_z_filt = filteredGyro[2];

    // ADXL377 
    SDDataLog.ADXL_acc_x = filteredADXL[0];
    SDDataLog.ADXL_acc_y = filteredADXL[1];
    SDDataLog.ADXL_acc_z = filteredADXL[2];

    // BMP280
    SDDataLog.BMP280_temp = bmpData.temperature;
    SDDataLog.BMP280_pres = bmpData.pressure;
    SDDataLog.BMP280_alt = bmpData.altitude;

    // NEO6M 
    //  ^ above 

    // Dead reckoning
    SDDataLog.DR_pos_x = pos[0];
    SDDataLog.DR_pos_y = pos[1];
    SDDataLog.DR_pos_z = pos[2];
    SDDataLog.DR_vel_x = vel[0];
    SDDataLog.DR_vel_y = vel[1];
    SDDataLog.DR_vel_z = vel[2];
    SDDataLog.DR_ori_x = ori[0];
    SDDataLog.DR_ori_y = ori[1];
    SDDataLog.DR_ori_z = ori[2];

    // Write to SD card
    logData();
    

/** Data transmission every third cycle */
    if ((cycleCounter % 3) == 0) {
        // Encode data as bytes: // most of this section was automatically generated by github copilot - incredible!
        // Status Code
        if (cycleCounter == 3) {
            Serial.printf("BMPAlt: %lf\n", bmpData.altitude);
            Serial.printf("DRZ: %lf\n", pos[3]);
            Serial.printf("absAcc: %lf\n", magnitude(filteredAccBNO055));
            Serial.printf("absVel: %lf\n", magnitude(vel));
            Serial.printf("GPS Lat, lon: %lf, %lf\n", GPSdata.lat, GPSdata.lon);
            Serial.printf("GPS Alt: %lf\n", GPSdata.alt);

        }
        byteArr[0] = DATA_CODE; 

        
        union byte_float_union {
            byte bytesFromFloat[4];
            float floatVal;
        };
        

        // BMP280  altitude
        float bmpAltTransmit = static_cast<float>(bmpData.altitude);
        // assign the bytes to the float
        byte_float_union bmpAltUnion;
        bmpAltUnion.floatVal = bmpAltTransmit;
        // copy the bytes to the byte array
        byteArr[1] = bmpAltUnion.bytesFromFloat[0];
        byteArr[2] = bmpAltUnion.bytesFromFloat[1];
        byteArr[3] = bmpAltUnion.bytesFromFloat[2];
        byteArr[4] = bmpAltUnion.bytesFromFloat[3];

        // Dead reckoning position Z
        short DRZ = static_cast<short>(pos[2]*10);
        byteArr[5] = DRZ >> 8;
        byteArr[6] = DRZ & 0xFF; // Big endian
        
        // Absolute Acceleration (BNO055 or ADXL)
        if (magnitude(filteredAccBNO055) > 14*9.81) { // over 14g, we use the ADXL377 data
            short absAccTransmit = static_cast<short>(magnitude(filteredADXL)*100);
            byteArr[7] = absAccTransmit >> 8;
            byteArr[8] = absAccTransmit & 0xFF; // Big endian :( 
        }   
        else {
            short absAccTransmit = static_cast<short>(magnitude(filteredAccBNO055)*100);
            byteArr[7] = absAccTransmit >> 8;
            byteArr[8] = absAccTransmit & 0xFF; // Big endian :( 
        }
        
        // Absolute Velocity (Dead reckoning)
        short absVelTransmit = static_cast<short>(magnitude(vel)*10);
        byteArr[9] = absVelTransmit >> 8;
        byteArr[10] = absVelTransmit & 0xFF; 

        // GPS latitiude
        float latTransmit = static_cast<float>(GPSdata.lat);
        byte_float_union latUnion;
        latUnion.floatVal = latTransmit;
        byteArr[11] = latUnion.bytesFromFloat[0];
        byteArr[12] = latUnion.bytesFromFloat[1];
        byteArr[13] = latUnion.bytesFromFloat[2];
        byteArr[14] = latUnion.bytesFromFloat[3];

        // byteArr[11] = (latTransmit >> 24) & 0xFF;
        // byteArr[12] = (latTransmit >> 16) & 0xFF;
        // byteArr[13] = (latTransmit >> 8) & 0xFF;
        // byteArr[14] = latTransmit & 0xFF;

        // GPS longitude
        float lonTransmit = static_cast<float>(GPSdata.lon);
        byte_float_union lonUnion;
        lonUnion.floatVal = lonTransmit;
        byteArr[15] = lonUnion.bytesFromFloat[0];
        byteArr[16] = lonUnion.bytesFromFloat[1];
        byteArr[17] = lonUnion.bytesFromFloat[2];
        byteArr[18] = lonUnion.bytesFromFloat[3];

        // byteArr[15] = (lonTransmit >> 24) & 0xFF;
        // byteArr[16] = (lonTransmit >> 16) & 0xFF;
        // byteArr[17] = (lonTransmit >> 8) & 0xFF;
        // byteArr[18] = lonTransmit & 0xFF;
        
        // GPS altitude
        float GPSaltTransmit = static_cast<float>(GPSdata.alt);
        byte_float_union GPSaltUnion;
        GPSaltUnion.floatVal = GPSaltTransmit;
        byteArr[19] = GPSaltUnion.bytesFromFloat[0];
        byteArr[20] = GPSaltUnion.bytesFromFloat[1];
        byteArr[21] = GPSaltUnion.bytesFromFloat[2];
        byteArr[22] = GPSaltUnion.bytesFromFloat[3];

        // byteArr[19] = (GPSaltTransmit >> 24) & 0xFF;
        // byteArr[20] = (GPSaltTransmit >> 16) & 0xFF;
        // byteArr[21] = (GPSaltTransmit >> 8) & 0xFF;
        // byteArr[22] = GPSaltTransmit & 0xFF;


        // Transmit byteArr
        unsigned long transmitTimoutMicros = micros();
        bool transmitTimeout = false;
        while (!transmittedFlag) {
            if (micros() - transmitTimoutMicros > 1000) { // 1ms timeout
                transmitTimeout = true;
                break;
            }
        }
        if (!transmitTimeout) {
            transmitData(byteArr);
        }


    }


/** Increment cycle counter */
    cycleCounter++; 

/** Ensuring cycles are 10ms long */
    unsigned long endOfLoopus = micros();
    if ((endOfLoopus-startOfLoopUs) < 10000) {
        delayMicroseconds(10000 - (endOfLoopus-startOfLoopUs));
    } // if the loop exceeded 10ms, there's nothing we can do. :(
}

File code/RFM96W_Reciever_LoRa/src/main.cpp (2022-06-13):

/*
   RadioLib SX127x Receive with Interrupts Example

   This example listens for LoRa transmissions and tries to
   receive them. Once a packet is received, an interrupt is
   triggered. To successfully receive data, the following
   settings have to be the same on both transmitter
   and receiver:
    - carrier frequency
    - bandwidth
    - spreading factor
    - coding rate
    - sync word

   Other modules from SX127x/RFM9x family can also be used.

   For default module settings, see the wiki page
   https://github.com/jgromes/RadioLib/wiki/Default-configuration#sx127xrfm9x---lora-modem

   For full API reference, see the GitHub Pages
   https://jgromes.github.io/RadioLib/
*/

#include <Arduino.h>
#include <RFM96WrecieveLORA.h>
#include "LineProtocolBuilder.h"

// Transmittsion/reception codes
#define RTC_SYNC_BYTE 0x99
#define TEST_CODE 0xAA
#define LAUNCH_COMMIT_CODE 0xBB
#define LAUNCH_COMMIT_CONFIRM 0xCC
#define DATA_CODE 0xDD


#define LAUNCH_COMMIT_BUTTON_PIN 3
#define RED_LED_PIN 4
#define GREEN_LED_PIN 5
byte rtcSynced = 0;
uint64_t unixTimeMs = 0; // the unix timestamp in milliseconds, synced by the rocket when it starts up.
uint32_t RTCsyncMillis = 0; // the millis() time we aquired the unixTime

char line[500] = "";
float prevGPSData[3] = {0, 0, 0};
int launched = 0;
int gpsLocked = 0;

char * uintToStr(  uint64_t num, char *str )
{
    uint8_t i = 0;
    uint64_t n = num;

    do
        i++;
    while ( n /= 10 );

    str[i] = '\0';
    n = num;

    do
        str[--i] = ( n % 10 ) + '0';
    while ( n /= 10 );

    return str;
}

void sendLaunchCommit() {
    Serial.println("Sending launch commit");


    // set up the ground station as a transmitter
    radio.setDio0Action(setFlag);
    byte arr[lenReceiveBytes] = {LAUNCH_COMMIT_CODE};
    int state = radio.startTransmit(arr, lenReceiveBytes);
    delay(200);
    // Set up ground station as a receiver
    radio.setDio0Action(setFlagRecieve);

    detachInterrupt(digitalPinToInterrupt(LAUNCH_COMMIT_BUTTON_PIN)); // So that we dont "launch commit twice"
    Serial.println("Succesfully sent launch commit and detatched interrupt");
    delay(100);
}

void setup() {
    Serial.begin(115200);
    RFM96WrecieveLORASetup();
    pinMode(LAUNCH_COMMIT_BUTTON_PIN, INPUT);
    pinMode(RED_LED_PIN, OUTPUT);
    pinMode(GREEN_LED_PIN, OUTPUT);
    digitalWrite(RED_LED_PIN, HIGH);
    digitalWrite(GREEN_LED_PIN, LOW);
    delay(500);
    attachInterrupt(digitalPinToInterrupt(LAUNCH_COMMIT_BUTTON_PIN), sendLaunchCommit, RISING);

    

}


void loop() {
    //Serial.println("\nReady to recieve");
    while (!receivedFlag); // wait for packet
    //Serial.println("Received packet");
    //Serial.println(millis());
    RFM96WrecieveBytesLORA();
    //Serial.println(byteArr[0], HEX);

    switch (byteArr[0]) {
        case RTC_SYNC_BYTE:{ 
            rtcSynced = 1;
            RTCsyncMillis = millis();
            for (int i=0; i<8; i++) {
                unixTimeMs |= ((uint64_t)byteArr[i+1]) << (7 * 8 - (i * 8));
            }
            Serial.println("\nRTC synced!");
            char unixTimeStr[20] = {0};
            uintToStr(unixTimeMs, unixTimeStr);
            Serial.println(unixTimeStr);   
            
            break; }
        case TEST_CODE: {
            // If there's a test code, we can test influx and Grafana as well
            uint64_t testTime = unixTimeMs + (millis() - RTCsyncMillis);
            char test1[20] = "";
            char test2[20] = "";
            char test3[20] = "";
            char test4[20] = "";
            char test5[20] = "";
            char test6[20] = "";
            char test7[20] = "";

            dtostrf(0, 7, 7, test1); // github copilot for the win
            dtostrf(1, 7, 7, test2);
            dtostrf(2, 7, 7, test3);
            dtostrf(3, 7, 7, test4);
            dtostrf(4, 7, 7, test5);
            dtostrf(5, 7, 7, test6);
            dtostrf(6, 7, 7, test7);
    
            char testTimeStr[20] = "";
            uintToStr(testTime, testTimeStr);
            if (rtcSynced) {
                sprintf(line, "Daedalus BMPAlt=%s,DRZ=%s,absAcc=%s,absVel=%s,GPSLat=%s,GPSLon=%s,GPSAlt=%s,launched=%d,gpsLocked=%d %s",
                        test1, test2, test3, test4, test5, test6, test7, launched, gpsLocked, testTimeStr);
            }
            else {
                sprintf(line, "Daedalus BMPAlt=%s,DRZ=%s,absAcc=%s,absVel=%s,GPSLat=%s,GPSLon=%s,GPSAlt=%s,launched=%d,gpsLocked=%d",
                        test1, test2, test3, test4, test5, test6, test7, launched, gpsLocked);
            }

            Serial.println(line);
            break; }
        case LAUNCH_COMMIT_CONFIRM: {
            Serial.println("\nLAUNCH COMMIT CONFIRMED\n");
            for (int i=0; i<lenReceiveBytes; i++) {
                Serial.print(byteArr[i], HEX);
                Serial.print(", ");
            }
            digitalWrite(RED_LED_PIN, LOW);
            digitalWrite(GREEN_LED_PIN, HIGH);
            break; }
        case DATA_CODE: {
            union byte_float_union {
                byte bytesFromFloat[4];
                float floatVal;
            };
            uint64_t timestamp = unixTimeMs + (millis() - RTCsyncMillis);
            byte_float_union bf;
            bf.bytesFromFloat[0] = byteArr[1];
            bf.bytesFromFloat[1] = byteArr[2];
            bf.bytesFromFloat[2] = byteArr[3];
            bf.bytesFromFloat[3] = byteArr[4];
            float BMP280Alt = bf.floatVal;

            float DRZ = ((byteArr[5] << 8) | (byteArr[6]) ) / 10.0;

            float absAcc = ((byteArr[7] << 8) | (byteArr[8]) ) / 100.0;

            float absVel = ((byteArr[9] << 8) | (byteArr[10]) ) /10; // not x10? ????? // TODO: investigate this

            bf.bytesFromFloat[0] = byteArr[11]; // github copilot saving my life again
            bf.bytesFromFloat[1] = byteArr[12];
            bf.bytesFromFloat[2] = byteArr[13];
            bf.bytesFromFloat[3] = byteArr[14];
            float GPSLat = bf.floatVal;

            bf.bytesFromFloat[0] = byteArr[15];
            bf.bytesFromFloat[1] = byteArr[16];
            bf.bytesFromFloat[2] = byteArr[17];
            bf.bytesFromFloat[3] = byteArr[18];
            float GPSLon = bf.floatVal;

            bf.bytesFromFloat[0] = byteArr[19];
            bf.bytesFromFloat[1] = byteArr[20];
            bf.bytesFromFloat[2] = byteArr[21];
            bf.bytesFromFloat[3] = byteArr[22];
            float GPSAlt = bf.floatVal;

            char BMP280AltStr[20] = "";
            char DRZStr[20] = "";
            char absAccStr[20] = "";
            char absVelStr[20] = "";
            char GPSLatStr[20] = "";
            char GPSLonStr[20] = "";
            char GPSAltStr[20] = "";
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

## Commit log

2022-02-15 Worked on calibration routine, refining dead reckoning.
2022-02-18 Added wiring, still to figure out the RF-LORA-915-D data protocol
    [Rocketry_circuit.sch]
2022-02-21 Wired in the RF-LORA-915-D - Over SPI
    [Rocketry_circuit.sch]
2022-02-23 Replaced NEO6M with NEO-M9N and wired it up.
    [Rocketry_circuit.sch]
2022-03-02 moved to circuitry folder
    [Rocketry_circuit.sch]
2022-03-02 moved to circuitry
2022-03-02 Updated library files (accuracy) and added 3D models. .brd file added
    [Rocketry_circuit.brd, Rocketry_circuit.sch]
2022-03-03 Commit before merging IMU reop
2022-03-10 Added 3D files and proper footprints for all components, worked on brd design
    [Rocketry_circuit.brd, Rocketry_circuit.sch]
2022-03-12 Commit before working on calibration routine
2022-03-12 Added rotation matrix function, working on calibration routine. - Currently the absolute value of acceleration is not equal to 9.8
2022-03-12 Accelerometer offsets/biases are now a constant value.
2022-03-14 Fixed rotation vector for world to relative coord frame
    [main.cpp]
2022-03-14 Working on calibration routine again, considering setting it constant.
2022-03-15 power circuitry up to date
    [Rocketry_circuit.brd, Rocketry_circuit.sch]
2022-03-18 updated board size to 31.75mm width, to fit into 34mm transition shoulder section
    [Rocketry_circuit.brd, Rocketry_circuit.sch]
2022-03-22 Incremental progress - 5V for GPS, interrupt wire, etc
    [Rocketry_circuit.brd, Rocketry_circuit.sch]
2022-03-26 performed testing on i2c read speeds - getAllData is buggy - dont use it
    [main.cpp]
2022-03-26 Updated i2c device to check for i2c availability, working on filtering.
2022-03-29 Working very well over FSK, bit rate of 300kbps - main issue is that writing to Serial takes a long time, something to consider for our ground station. LoRa might work OK after all - looks like Seria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
    [main.cpp]
2022-03-30 added a transisor and breakouts for spare teensy pins (incase we need them)
    [Rocketry_circuit.brd, Rocketry_circuit.sch]
2022-03-30 added ADXL code, looks like it really needs that capacitor to smooth things over. /:)
2022-03-31 beginning to think LoRa is too slow - testing commit
    [main.cpp]
2022-03-31 LoRa is too slow - 121ms for a packet of any length, using interrupt based method.
    [main.cpp]
2022-04-04 fixed calcRotationVect functionality - orientaion needs to be anticlockwise->increasing!
    [main.cpp]
2022-04-04 Implemented integration of gyroscopes - still need to do reference frame transfer and investigate higher update rates
2022-04-04 i2c read time is now at 3.8ms max ????? - very odd behaviour. turns our getAllData was fine all along ??
2022-04-04 implemented first order hold on gyroscope integration
2022-04-04 Implemented first order hold on position and velocity.
2022-04-04 fixed offsets, implemented dead reckoning - Lots of drift - may only be accurate for flight? - work to be done
    [main.cpp]
2022-04-06 LoRa has much better range - working on optimisation - currently aas 64ms between writes.
2022-04-06 Lora is just too slow - Using FSK instead.
    [main.cpp]
2022-04-09 Final sch and brd files - Ordered pcb
    [Rocketry_circuit.brd, Rocketry_circuit.sch]
2022-04-09 Drift on position is huge - Double integration of acceleration and integration of gyros given massive errors - Considering sensor fusion - Also considering running algo at 400Hz (2.5ms cycle time)
    [main.cpp]
2022-04-12 Experimenting with live accelerometer and gyroscope bias estimation.
2022-04-12 live bias estimation is tricky - not sure why it's not working - needs a proper dry run
    [main.cpp]
2022-04-18 added sch, brd, and final production images of pcb
2022-04-27 down to 58ms transmit time at spreading factor of 6, but it doesnt recieve correctly??? - need to do range testing.
    [main.cpp]
2022-04-28 Added final pcb images
2022-05-03 added teensyRTC code
2022-05-03 added teensyRTC.cpp and teensyRTC.h
2022-05-04 - Added Ash's fancy RTC code - Now re-fixes in 2 seconds. - Fixed getUBX, now the single polling commands work. - Altered GPSweek() and actualTimeOfWeekms() to use ethe getTimeStampMillis() function
    [NEO6mWithAssistNow.cpp, assistNow.h, main.cpp]
2022-05-07 Fixed header files. - must use spreading factor 8 - 175666us (17.6ms) before ready to re-transmit.
    [RFM96WtransmitLORA.cpp, main.cpp]
2022-05-07 fixed getADXL377 so it now returns a Vector<double>. Added offsets manually.
    NOTES: The sensor seems very noisy when still, but performs well under higher acceleration, which is what we need it for.
    [ADXL377.cpp]
2022-05-11 tested acquisition time and fixed setup - 175us every time
    [main.cpp]
2022-05-14 changed timestamp to uint_64 - rb.printf-ing with %llu
2022-06-02 added ground station RTC sync and updated data logging struct
2022-06-04 Fixed offset finding and calibration routine for a known flat and stable surface - Now very accurate :)
    [BNO055daedalus.cpp, main.cpp]
2022-06-06 Increased gpsSerial BAUD rate, and fixed some config errors. - Note that the 'quick' way to get GPS data is to send the NAV_POSLLH UBX command ~200ms before you actually need it.
    [NEO6mWithAssistNow.cpp, main.cpp]
2022-06-07 Implemented sending "Launch commit" with the big red button and receiving confirmation message - with LEDs!
2022-06-10 Added parsing of data for Grafana, fixed buggy transmission.
    [ADXL377.cpp, BNO055daedalus.cpp, NEO6mWithAssistNow.cpp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]
2022-06-11 Added ADXL377 bias calculation - Surprisingly good with the kalman filter - NOTE: MUST be done after all the other components have been switched on to simulate the same current draw conditions (ADXL3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
2022-06-11 Fixed getInitialOrientation - now gets very accurate orientation when on the launch rail - works best with a bias-compensated sensor.
    [BNO055daedalus.cpp, main.cpp]
2022-06-13 added launch rail photo
